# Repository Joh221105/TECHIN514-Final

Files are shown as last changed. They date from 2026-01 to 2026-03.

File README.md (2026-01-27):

# Bloop
An interactive desk companion featuring a magnetically-controlled ferrofluid that responds to hand gestures (and potentially audio commands in the future). The creature exhibits lifelike behaviors through computer vision and wireless control. Core Behaviors:

Follow - Tracks and follows user's face position
Hide - Rotates away from user (shy behavior)
Spin - Runs around the track once

Sketch of the overview of overall product

### Physical Features
A circular acrylic platform (12" diameter) contains ferrofluid in carved tracks. Beneath the platform, a stepper motor controls an arm with an embedded magnet rotates to manipulate the fluid. An LED ring provides ambient lighting and behavioral feedback.

# Sensor Device

### ESP32-C3
The sensing device uses an ESP32C3 with a SEN0359-EN voice recognition module to detect command words and move the stepper motor accordingly to make the ferrofluid perform the "tricks".

The device is powered by a 150mAh 3.7V LiPo battery with USB charging, making it portable and easily repositionable. 

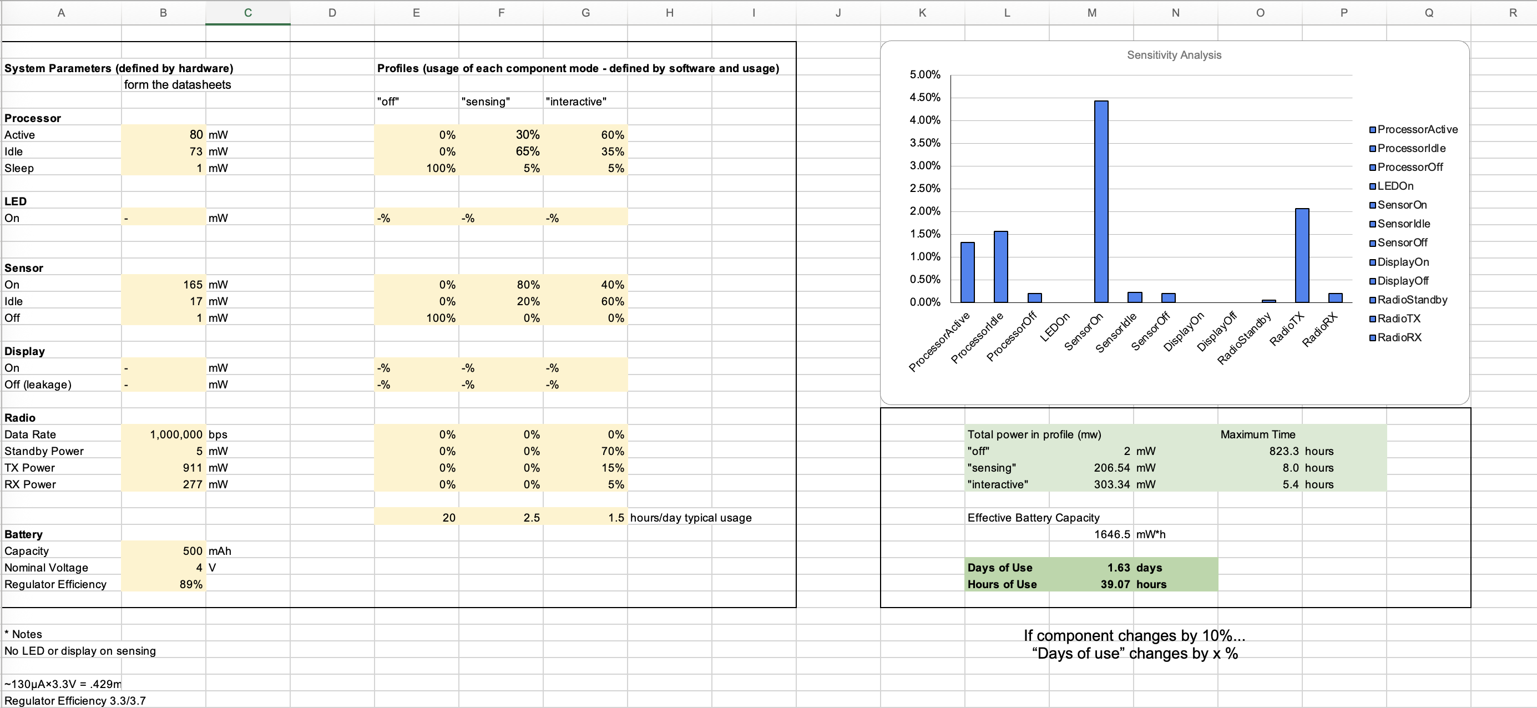
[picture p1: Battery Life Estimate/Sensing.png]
Sketch of sensing device


# Display Device

### Magnetically-Actuated Ferrofluid Platform
The display device features a laser-cut circular acrylic platform with ferrofluid in carved tracks. A NEMA 17 stepper motor beneath the platform rotates a vertical arm assembly, positioning a neodymium magnet 1-2mm under the ferrofluid. The TMC2208 driver provides silent operation with microstepping for smooth, organic motion.

An ESP32-C3 microcontroller receives wireless commands and controls motor movements. A WS2812B LED ring (16 LEDs) provides visual feedback with color-coded patterns. A capacitive touch pad enables power control, and an 11.1V 2200mAh LiPo battery provides power and allows portability.

As the magnet rotates, the ferrofluid forms dramatic spikes that follow the magnetic field, creating lifelike tracking behaviors that respond to user movements detected by the camera.

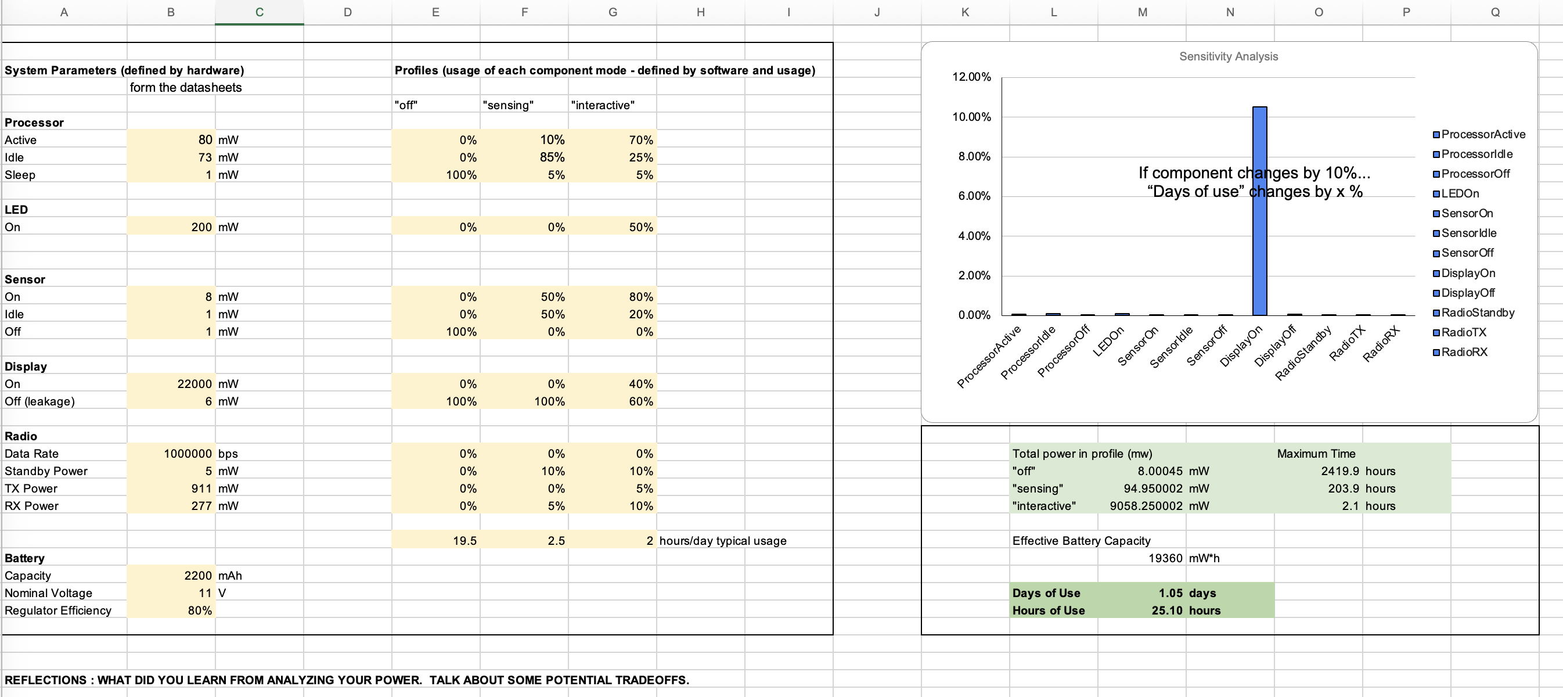
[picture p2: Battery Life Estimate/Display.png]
Sketch of the display device


# Communication Between Devices

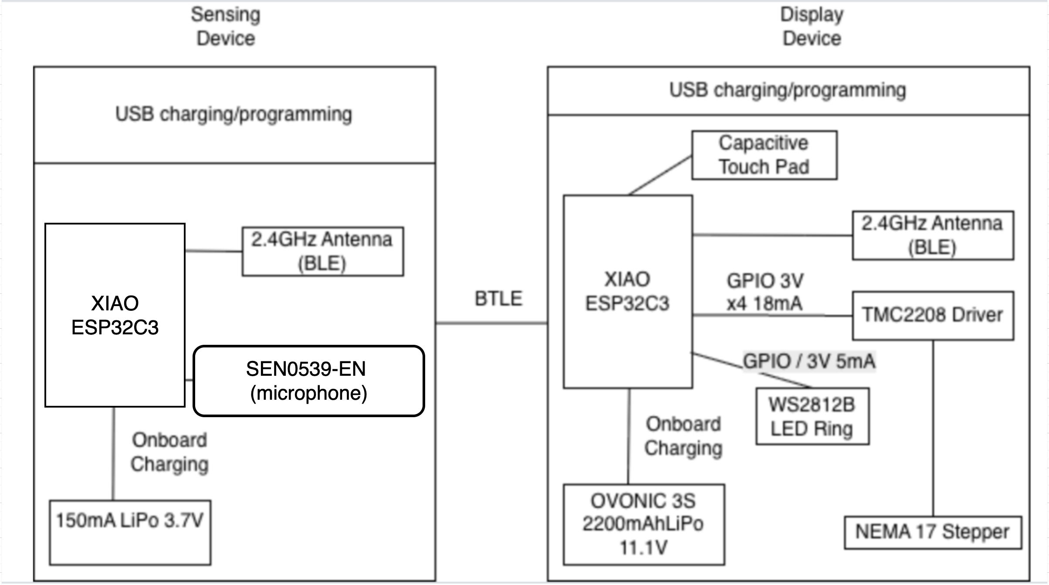
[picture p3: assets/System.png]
Systems Diagram

Flow chart

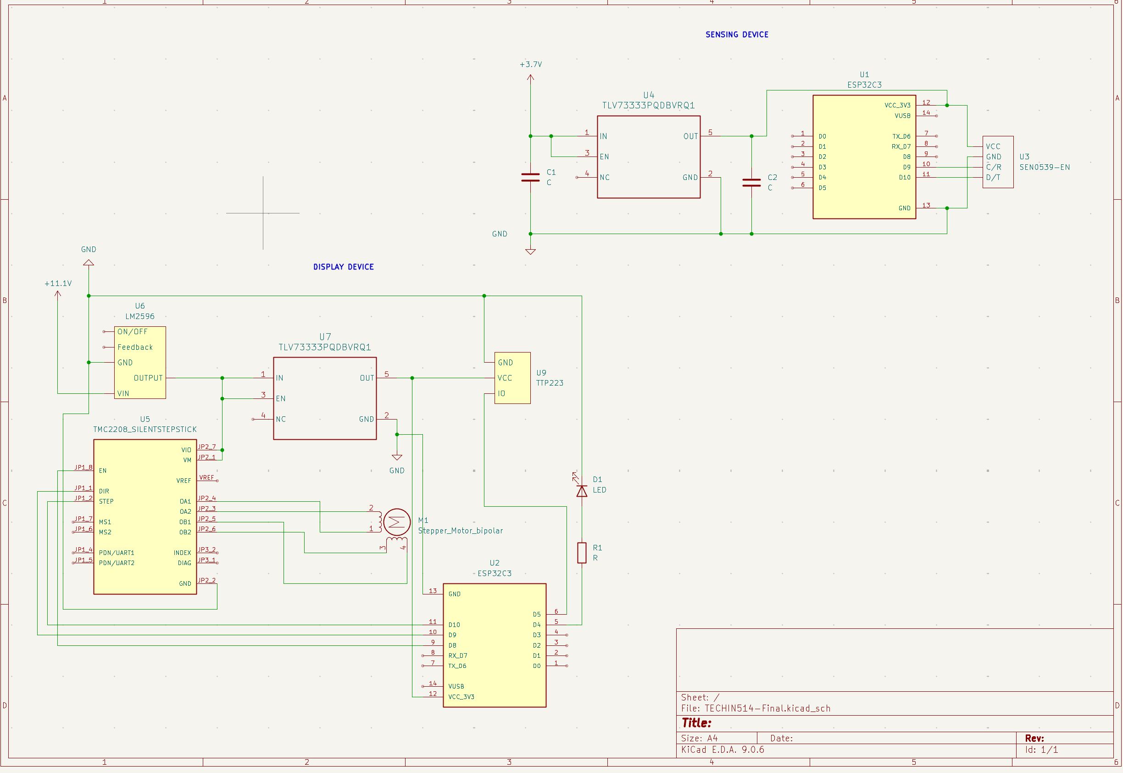
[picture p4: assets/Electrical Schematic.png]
Electrical Diagram


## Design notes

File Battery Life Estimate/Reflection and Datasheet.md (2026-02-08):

# Sensing Device

### How did you determine your "days of use" metric?
The days of use are based on an estimate of a realistic daily usage scenario for an interactive pet toy. I estimated the device spends 20 hours in off mode/deep sleep, 2.5 hours in sensing mode (listening for wake word and voice commands spread throughout the day), and 1.5 hours in interactive mode (actively sending BLE commands to the display device after recognizing a command). This models someone interacting with the pet a few times throughout the day in short sessions. 

### What do you think is the optimum battery size?
A 500mAh 3.7V LiPo is a good fit, it is enough to push the usage to over 24 hours and some spare just in case usage is higher than expected. It is also compact and light enough to make sense for the sensing device. 

### Hardware/software/cost/effort tradeoffs to improve UX?
One tradeoff would be adding a simple analog audio sensor that detects sound energy before powering on the voice module, this way the module only draws power when someone is actually speaking nearby, rather than continuously listening, which then means we can decrease the size of the battery and weight. On the software side, implementing smarter I2C polling intervals could reduce the ESP32-C3's active duty cycle during sensing mode, which would cut processor active time significantly with only a slight delay in responsiveness. For BLE, using longer connection intervals would reduce radio power during interactive mode, but can slow down command time.
<hr>

# Display Device

### How did you determine your "days of use" metric?
The display device follows a 19.5 hours off, 2.5 hours in sensing (awake and listening for BLE commands), and 2 hours in interactive mode (motor movements, LED effects, and capacitive touch sensor). The interactive time is longer because the motor movements and LED animations take time to execute. For instance a single "Run a Lap" command might run the stepper motor for 10-15 seconds. 

### What do you think is the optimum battery size?
The OVONIC 3S 2200mAh 11.1V LiPo is good enough because the TMC2208 stepper driver and NEMA 17 motor perform best at higher voltages for torque and speed, which would be required to move the magnet on top of the gauge needle. The bulkiness and weight of the battery doesn’t matter as much since the display device is meant to be stationary. 

### Hardware/software/cost/effort tradeoffs to improve UX?
The biggest tradeoff is the stepper motor power consumption. TMC2208 gives silent operation which is great for a pet toy, however other drivers might be more efficient at the cost of louder motor movements.The LED brightness could also be decreased with minimal impact on user experience, however it can also decrease power consumption. A smaller stepper motor would use less power but might not have enough torque to reliably move the aluminum arm through the ferrofluid.

# Data Sheets

Processor: https://files.seeedstudio.com/wiki/XIAO_WiFi/Resources/esp32-c3_datasheet.pdf

Sensor
https://wiki.dfrobot.com/sku_sen0539-en_gravity_voice_recognition_module_i2c_uart

Motor: 
https://www.omc-stepperonline.com/download/17HS19-2004S1.pdf

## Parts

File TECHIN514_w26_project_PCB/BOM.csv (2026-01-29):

# | Reference | Qty | Value | Footprint | DNP
1 | C1, C2 | 2 | 1µF | Capacitor_SMD:C_0402_1005Metric_Pad0.74x0.62mm_HandSolder
2 | C3 | 1 | 100nF | Capacitor_SMD:C_0402_1005Metric_Pad0.74x0.62mm_HandSolder
3 | C4 | 1 | 4.7µF | Capacitor_SMD:C_0402_1005Metric_Pad0.74x0.62mm_HandSolder
4 | D1 | 1 | LED | LED_SMD:LED_0402_1005Metric_Pad0.77x0.64mm_HandSolder
5 | J1 | 1 | Conn_01x04_Pin | Connector_PinSocket_2.54mm:PinSocket_1x04_P2.54mm_Vertical
6 | R1 | 1 | 1kΩ | Resistor_SMD:R_0402_1005Metric_Pad0.72x0.64mm_HandSolder
7 | R2, R3, R4 | 3 | 10kΩ | Resistor_SMD:R_0402_1005Metric_Pad0.72x0.64mm_HandSolder
8 | U1 | 1 | VL53L4CXV0DH_1 | L3KicadFoot:XCDR_VL53L4CXV0DH_1
9 | U2 | 1 | MIC5376-2.8YMT-TZ | L3KicadFoot:SC-70_C5_MCH-L

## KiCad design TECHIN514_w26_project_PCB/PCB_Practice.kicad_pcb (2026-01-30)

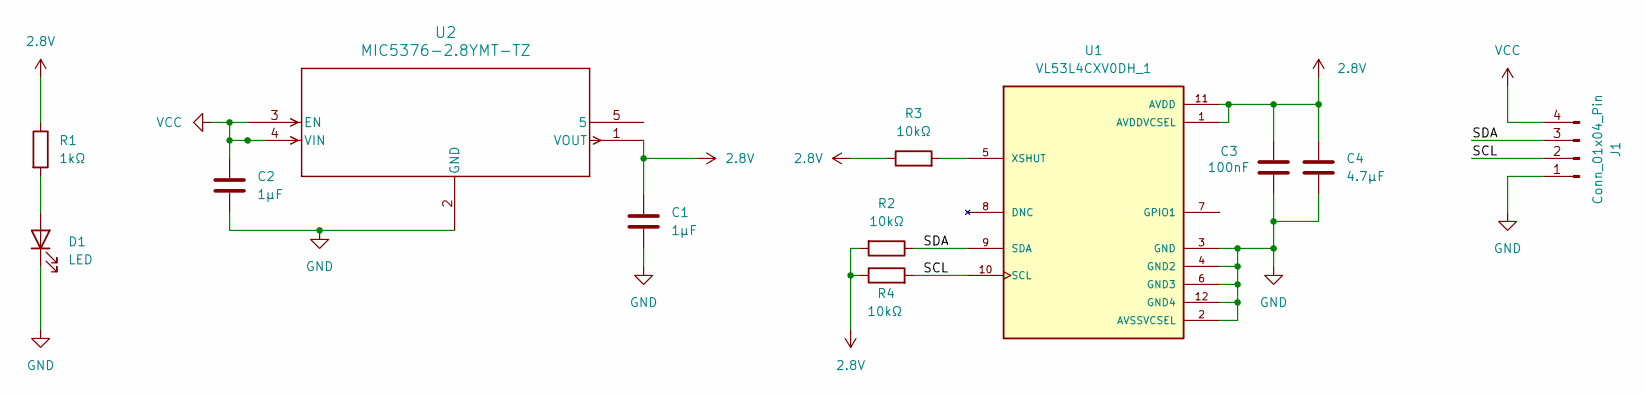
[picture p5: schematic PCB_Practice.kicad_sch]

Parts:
C1, C2: 1µF; C_0402_1005Metric_Pad0.74x0.62mm_HandSolder
C3: 100nF; C_0402_1005Metric_Pad0.74x0.62mm_HandSolder
C4: 4.7µF; C_0402_1005Metric_Pad0.74x0.62mm_HandSolder
D1: LED; LED_0402_1005Metric_Pad0.77x0.64mm_HandSolder
J1: Conn_01x04_Pin; PinSocket_1x04_P2.54mm_Vertical
R1: 1kΩ; R_0402_1005Metric_Pad0.72x0.64mm_HandSolder
R2, R3, R4: 10kΩ; R_0402_1005Metric_Pad0.72x0.64mm_HandSolder
U1: VL53L4CXV0DH_1; XCDR_VL53L4CXV0DH_1; PARTREV 4
U2: MIC5376-2.8YMT-TZ; SC-70_C5_MCH-L

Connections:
2.8V: C1.1, C3.1, C4.2, R1.1, R2.2, R3.1, R4.1, U1.1 (AVDDVCSEL), U1.11 (AVDD), U2.1 (VOUT)
/SCL: J1.2, R4.2, U1.10 (SCL)
/SDA: J1.3, R2.1, U1.9 (SDA)
GND: C1.2, C2.2, C3.2, C4.1, D1.1 (K), J1.1, U1.2 (AVSSVCSEL), U1.3 (GND), U1.4 (GND2), U1.6 (GND3), U1.12 (GND4), U2.2 (GND)
unnamed: D1.2 (A), R1.2
unnamed: R3.2, U1.5 (XSHUT)
VCC: C2.1, J1.4, U2.3 (EN), U2.4 (VIN)

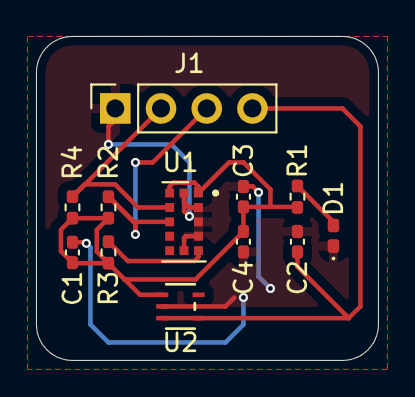
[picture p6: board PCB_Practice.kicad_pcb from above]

Board: 2 copper layers, 19.0 x 18.0 mm, 12 parts (0 on the bottom side), 7 nets.

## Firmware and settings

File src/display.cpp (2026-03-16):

#include <Arduino.h>
#include "DFRobot_DF2301Q.h"
#include <BLEDevice.h>
#include <BLEServer.h>
#include <BLEUtils.h>
#include <BLE2902.h>

// ── UART Pins ──────────────────────────────────────────────────────────────
HardwareSerial sensorSerial(1);
DFRobot_DF2301Q_UART asr(&sensorSerial, D10, D9);

// ── BLE UUIDs ──────────────────────────────────────────────────────────────
#define SERVICE_UUID        "1a8ac0fb-de23-4540-9511-a4fa87aaab90"
#define CHARACTERISTIC_UUID "1a8ac0fb-de23-4540-9511-a4fa87aaab91"
#define DEVICE_NAME         "SensorESP32"

// ── Globals ────────────────────────────────────────────────────────────────
BLEServer*         pServer         = nullptr;
BLECharacteristic* pCharacteristic = nullptr;
bool deviceConnected    = false;
bool oldDeviceConnected = false;

// ── Sliding Window Histogram ───────────────────────────────────────────────
#define HISTORY_SIZE 10
#define HISTORY_WINDOW_MS 5000
#define COOLDOWN_MS 1500

struct CMDEvent { uint8_t id; unsigned long t; };
CMDEvent history[HISTORY_SIZE];
int historyIdx = 0;

uint8_t lastSentID = 0;
unsigned long lastSentTime = 0;

void recordCMD(uint8_t id) {
  history[historyIdx] = { id, millis() };
  historyIdx = (historyIdx + 1) % HISTORY_SIZE;
}

uint8_t countRecent(uint8_t id) {
  unsigned long now = millis();
  uint8_t count = 0;
  for (int i = 0; i < HISTORY_SIZE; i++) {
    if (history[i].id == id && (now - history[i].t) < HISTORY_WINDOW_MS)
      count++;
  }
  return count;
}

uint8_t filteredCMDID(uint8_t id) {
  if (id == 0) return 0;
  unsigned long now = millis();
  if (id == lastSentID && (now - lastSentTime) < COOLDOWN_MS) return 0;
  lastSentID = id;
  lastSentTime = now;
  recordCMD(id);
  return id;
}

// ── BLE Server Callbacks ───────────────────────────────────────────────────
class ServerCallbacks : public BLEServerCallbacks {
  void onConnect(BLEServer* pServer) override {
    deviceConnected = true;
    Serial.println("[BLE] Display connected");
  }
  void onDisconnect(BLEServer* pServer) override {
    deviceConnected = false;
    Serial.println("[BLE] Display disconnected");
  }
};

// ── Setup ──────────────────────────────────────────────────────────────────
void setup() {
  Serial.begin(115200);
  delay(500);
  Serial.println("Starting...");

  memset(history, 0, sizeof(history));

  if (!asr.begin()) {
    Serial.println("asr.begin() FAILED - check wiring!");
  } else {
    Serial.println("asr.begin() SUCCESS");
    delay(500);
    asr.settingCMD(DF2301Q_UART_MSG_CMD_SET_MUTE, 1);
    delay(100);
    asr.settingCMD(DF2301Q_UART_MSG_CMD_SET_MUTE, 0);
    delay(100);
    asr.settingCMD(DF2301Q_UART_MSG_CMD_SET_VOLUME, 1);
    delay(100);
    asr.settingCMD(DF2301Q_UART_MSG_CMD_SET_WAKE_TIME, 30);
  }

  BLEDevice::init(DEVICE_NAME);
  pServer = BLEDevice::createServer();
  pServer->setCallbacks(new ServerCallbacks());

  BLEService* pService = pServer->createService(SERVICE_UUID);
  pCharacteristic = pService->createCharacteristic(
    CHARACTERISTIC_UUID,
    BLECharacteristic::PROPERTY_READ | BLECharacteristic::PROPERTY_NOTIFY
  );
  pCharacteristic->addDescriptor(new BLE2902());

  uint8_t initVal = 0;
  pCharacteristic->setValue(&initVal, 1);
  pService->start();

  BLEAdvertising* pAdvertising = BLEDevice::getAdvertising();
  pAdvertising->addServiceUUID(SERVICE_UUID);
  pAdvertising->setScanResponse(true);
  pAdvertising->setMinPreferred(0x06);
  BLEDevice::startAdvertising();
  Serial.println("[BLE] Advertising as 'SensorESP32'");
}

// ── Loop ───────────────────────────────────────────════════════════════════
void loop() {
  uint8_t id = filteredCMDID(asr.getCMDID());
  while (asr.getCMDID() != 0) {}  // drain buffer of duplicates

  if (id != 0) {
    Serial.print("Command ID: ");
    Serial.println(id);

    pCharacteristic->setValue(&id, 1);
    if (deviceConnected) {
      pCharacteristic->notify();
      Serial.println("[BLE] Notification sent");
    }
  }

  // ── BLE reconnect ─────────────────────────────────────────────────────
  if (!deviceConnected && oldDeviceConnected) {
    delay(500);
    pServer->startAdvertising();
    Serial.println("[BLE] Restarting advertising...");
    oldDeviceConnected = deviceConnected;
  }
  if (deviceConnected && !oldDeviceConnected) {
    oldDeviceConnected = deviceConnected;
  }

  delay(100);
}

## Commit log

2026-01-27 update architectural system and add electrical diagram
    [TECHIN514-Final.kicad_sch]
2026-01-29 add kicad files for pcb design lab 3
    [BOM.csv, PCB_Practice.kicad_pcb, PCB_Practice.kicad_sch]
2026-01-30 add ground plane to back of pcb
    [PCB_Practice.kicad_pcb]
2026-02-08 add Battery Life Estimate assignment
    [Display.xlsx, Sensing.xlsx]
2026-03-02 add src folder with current sensor and display code
2026-03-16 add updated display and sensor code
